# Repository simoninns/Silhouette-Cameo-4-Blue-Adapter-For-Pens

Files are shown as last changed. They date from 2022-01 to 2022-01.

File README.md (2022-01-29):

# Silhouette Cameo 4 Blue Adapter For Pens
## Overview
This is a 3D printable adapter for the Silhouette Cameo 4 equivalent to the blue adapter typically used to allow Silhouette pens to work in the Cameo 4 (why they don't work natively is anyone's guess...).

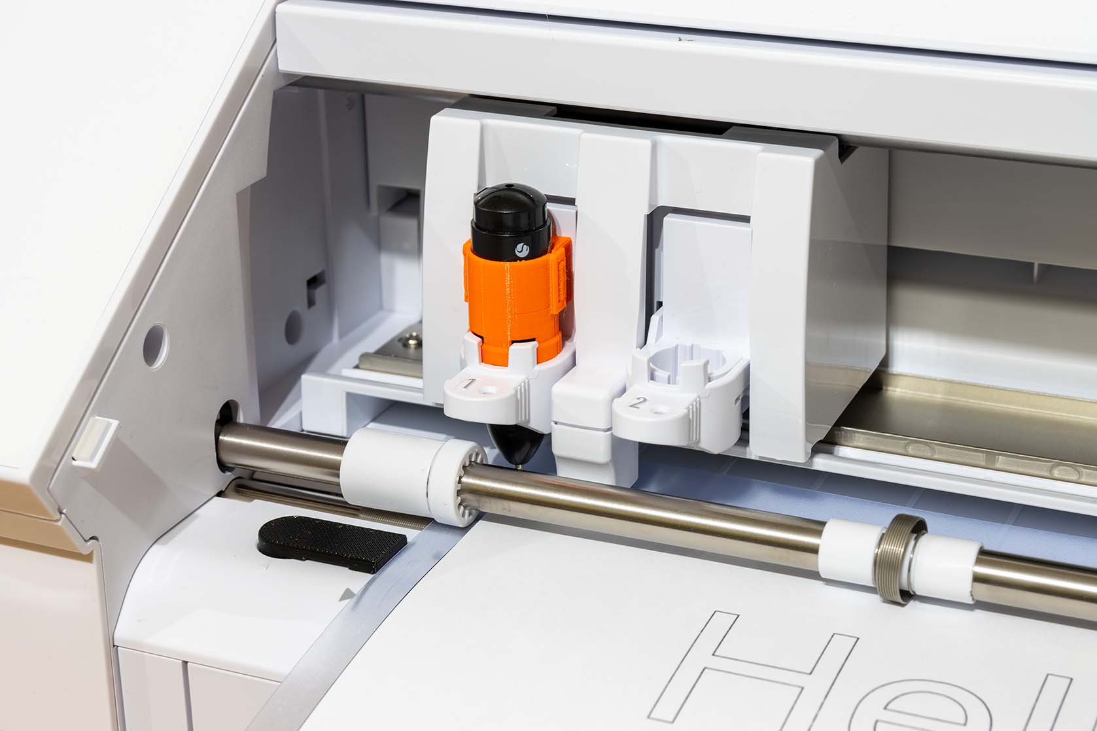
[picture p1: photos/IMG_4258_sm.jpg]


Since the original adapter is made from extremely thin plastic it is not possible to print the adapter without redesign.  This design relies on front and back guide pins to hold the pen square to the plotter rather than a thin plastic surround.  The pen is held rigidly and does not wobble during plotting. 

To make the design even more convenient there is a pen lid included so the pen does not need to be removed from the adapter when not in use; simply pop on the cap and store.

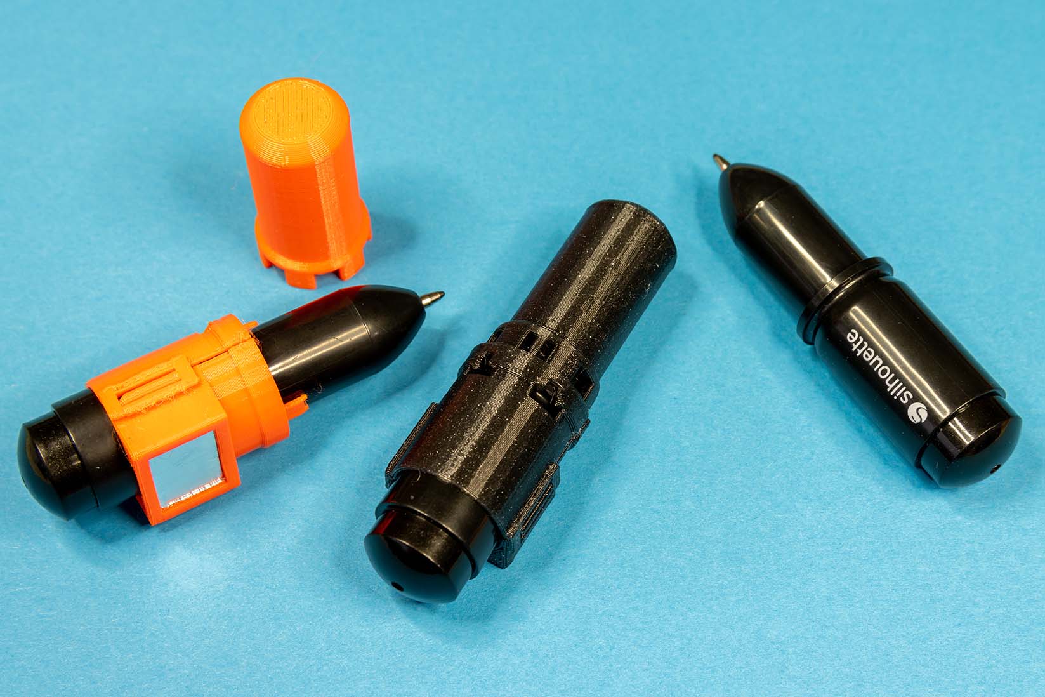
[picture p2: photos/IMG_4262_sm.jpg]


Note: This project is GPLv3 open-source. The github repository for the model (containing the complete OpenSCAD project) can be found at https://github.com/simoninns/silhouette-cameo-4-blue-adapter-for-pens

## Printing instructions
The model has been printed and tested on the Prusa MK3S/MMU2S printer using Prusament PETG filament. All parts fit on a 20x20 printing bed.

### Recommended print settings

Print settings (for Prusa Slicer) are the same for all included parts:

* Material: PETG
* Layer: 0.20mm (Quality)
* Infill: 15%
* Supports: No Supports

Note that the upper 'ring' of the front and back parts may string a little due to the lack of supports.  Simply trim this off after printing rather than using build-plate supports for quicker printing with less material.

## Assembly
Place the front part over the pen ensuring that the 'ring' is correctly seated. Then clip the back part in place one side at a time.  Finally, pop the cap on the top.  Now follow the tool auto-detection instructions below.

## Tool auto-detection
The Cameo 4 uses an automatic tool detection system which is based on the size of a rectangle of aluminum on the back of the tool.  The pen-holder design has a 14x10mm recess for the aluminum.

A Silhouette Studio file is included in the project that can be used to make the required aluminum.  Use 50mm wide aluminum tape (I used Tesa professional aluminum tape (strong) which is 50mm x 25m x 50 microns).  Aluminum tape is used in the heating/air con. industry so it's easy to source.

The included file uses the auto-blade with the following settings:

* Blade Depth: 4
* Force: 14
* Passes: 1
* Speed: 5

Simply cut about 150mm of aluminum tape and affix to a cutting board (make sure it's as smooth as possible). Then, after cutting, place 1 or 2 pieces (one on top of the other) in the provided recess on the tool.  The Cameo will then auto-detect the pen holder just like the manufacturer's original part.

## Author
The Silhouette Cameo 4 Blue Adapter For Pens is designed and maintained by Simon Inns.

# Licensing
## OpenSCAD source files - software license (GPLv3)

    This is free software: you can redistribute it and/or modify
    it under the terms of the GNU General Public License as published by
    the Free Software Foundation, either version 3 of the License, or
    (at your option) any later version.
    
    This program is distributed in the hope that it will be useful,
    but WITHOUT ANY WARRANTY; without even the implied warranty of
    MERCHANTABILITY or FITNESS FOR A PARTICULAR PURPOSE.  See the
    GNU General Public License for more details.
    
    You should have received a copy of the GNU General Public License
    along with this program.  If not, see <http://www.gnu.org/licenses/>.

## Non-source-code media - Creative Commons license (Creative Commons BY-SA 4.0)
Please see the following link for details: https://creativecommons.org/licenses/by-sa/4.0/

You are free to:

Share - copy and redistribute the material in any medium or format
Adapt - remix, transform, and build upon the material
for any purpose, even commercially.

This license is acceptable for Free Cultural Works.

The licensor cannot revoke these freedoms as long as you follow the license terms.

Under the following terms:

Attribution - You must give appropriate credit, provide a link to the license, and indicate if changes were made. You may do so in any reasonable manner, but not in any way that suggests the licensor endorses you or your use.

ShareAlike - If you remix, transform, or build upon the material, you must distribute your contributions under the same license as the original.

No additional restrictions - You may not apply legal terms or technological measures that legally restrict others from doing anything the license permits.

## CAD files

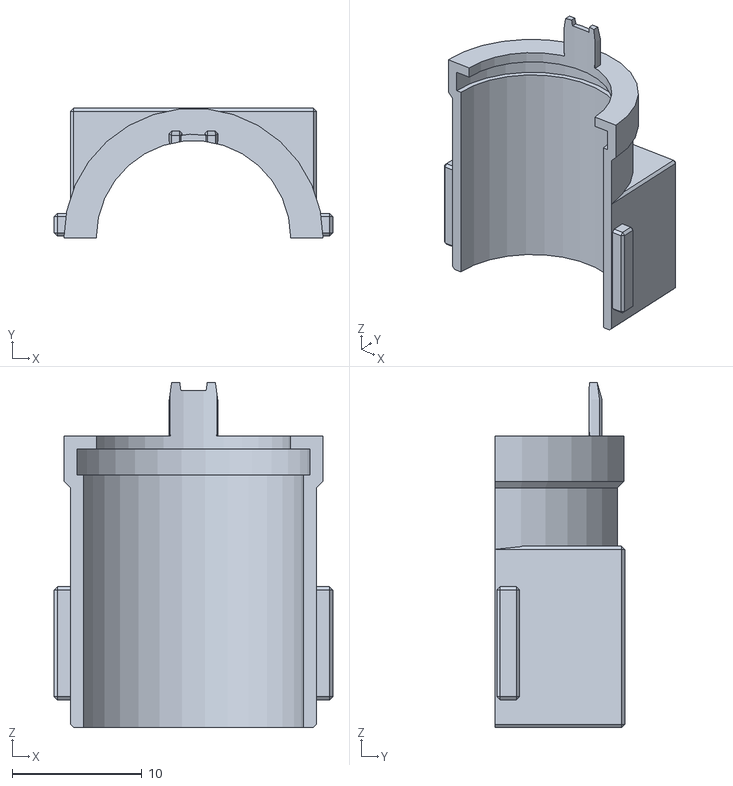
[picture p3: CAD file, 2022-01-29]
stl/blue_front.stl
21.5 x 10.0 x 26.6

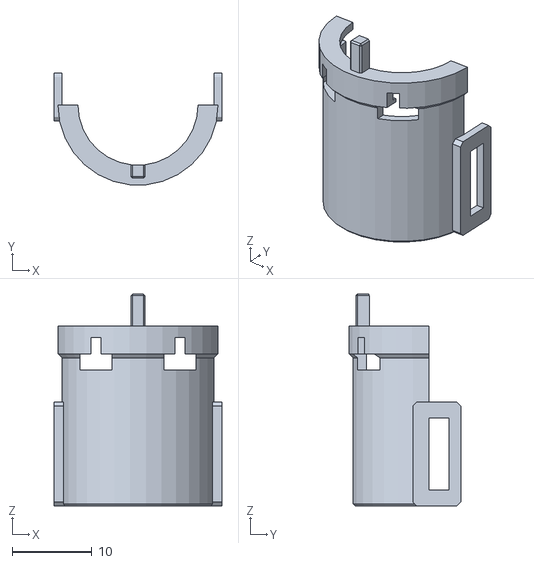
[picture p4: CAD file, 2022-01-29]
stl/blue_back.stl
21.0 x 13.9 x 26.5

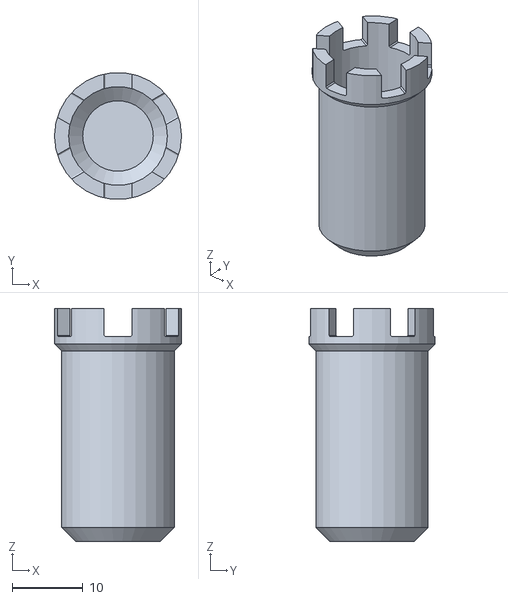
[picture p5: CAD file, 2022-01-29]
stl/blue_lid.stl
18.0 x 17.9 x 33.0

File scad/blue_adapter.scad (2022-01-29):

/************************************************************************

    blue_adapter.scad
    
    Silhouette Cameo 4 Adapters
    Copyright (C) 2022 Simon Inns
    
    This is free software: you can redistribute it and/or modify
    it under the terms of the GNU General Public License as published by
    the Free Software Foundation, either version 3 of the License, or
    (at your option) any later version.
    
    This program is distributed in the hope that it will be useful,
    but WITHOUT ANY WARRANTY; without even the implied warranty of
    MERCHANTABILITY or FITNESS FOR A PARTICULAR PURPOSE.  See the
    GNU General Public License for more details.
    
    You should have received a copy of the GNU General Public License
    along with this program.  If not, see <http://www.gnu.org/licenses/>.
	
    Email: simon.inns@gmail.com
    
************************************************************************/

include <BOSL/constants.scad>
use <BOSL/transforms.scad>
use <BOSL/shapes.scad>

module insertion_guide_front()
{
    // Insert guides
    move([0,7.75,27.5]) hull() {
        move([0,0,-4]) cuboid([1,1,4], chamfer=0.2);
        move([0,-0.5,-1]) cuboid([1.25 / 2,2.5 / 2,0.25]);
    }
}

module insertion_guide_back()
{
    // Insert guides
    move([0,-8,24]) cuboid([1.75,2.25,5], chamfer=0.2);
}

module tool_lock()
{
    difference() {
        union() {
            move([0,0,2.5]) {
                move([+5.25,0,21.5 - 4]) cuboid([1.25, 20, 2.1]);
                move([-5.25,0,21.5 - 4]) cuboid([1.25, 20, 2.1]);
            }

            move([0,0,17]) tube(h=2, od=20, , id=14, center=false);
        }

        move([0,0,17]) cuboid([6.5, 20, 6]);
        move([+10.5,0,17]) cuboid([6.5, 20, 6]);
        move([-10.5,0,17]) cuboid([6.5, 20, 6]);
        move([0,7,19]) cuboid([20, 10, 6]);
    }
}

module holder_body()
{
    // Base of holder
    difference() {
        union() {
            move([0,20/4,7]) cuboid([19,20/2,14], chamfer=0.25, edges=EDGES_TOP+EDGES_BOTTOM+EDGES_BACK);
            cyl(h=22.5, d=19, center=false, chamfer=0.25);

            move([0,0,16]) cyl(h=6.5, d=20, center=false, chamfer1=3);
        }

        move([0,10,14/2]) cuboid([14.2,2,10.2], edges=EDGES_TOP); // Alu marker recess
        tool_lock();
    }

    // Main Shaft
    move([0,0,21.5]) zrot(80) pie_slice(ang=20, l=4.5, d=16);
}

module inner_profile()
{
    // Base
    move([0,0,9 - 1]) cyl(h=24, d=17);

    // Ring
    move([0,0,20.5]) cyl(h=2, d=18);

    // Top
    move([0,0,17]) cyl(h=51, d=15);
}

module front_catches()
{
    move([-11 + 0.25,0.125,2.125]) cuboid([1.5,1.75,8.75], center=false, chamfer=0.25, edges=EDGES_X_ALL+EDGES_LEFT);
    move([9.25,0.125,2.125]) cuboid([1.5,1.75,8.75], center=false, chamfer=0.25, edges=EDGES_X_ALL+EDGES_RIGHT);
}

module back_catches()
{
    move([-14.5,-1,0]) {
        difference() {
            move([0,-1,0]) cuboid([1,6,13], center=false, chamfer=0.5, edges=EDGES_X_ALL);
            move([-1,1,2]) cuboid([3,2.5,9], center=false);
        }

        move([-0.75,-1,0]) cuboid([0.75,2,13], center=false, chamfer=0.5, edges=EDGES_X_FR);
    }

    move([-34.5,-1,0]) {
        difference() {
            move([0,-1,0]) cuboid([1,6,13], center=false, chamfer=0.5, edges=EDGES_X_ALL);
            move([-1,1,2]) cuboid([3,2.5,9], center=false);
        }

        move([0.75,-1,0]) cuboid([0.75,2,13], center=false, chamfer=0.5, edges=EDGES_X_FR);
    }
}

module render_blue_adapter_front(isDisplay)
{
    posy = isDisplay ? 0:6;

    move([0,posy,0]) {
        difference() {
            holder_body();
            inner_profile();

            // Cross section
            move([0,-10,25]) cuboid([20,20,60]);
        }

        // Insertion guides
        difference() {
            union () {
                move([+1.25 + 0.125,0,0]) insertion_guide_front();
                move([-1.25 - 0.125,0,0]) insertion_guide_front();
            }

            move([0,0,17]) cyl(h=51, d=15);
        }

        front_catches();
    }
}

module render_blue_adapter_back(isDisplay)
{
    posy = isDisplay ? 0:-6;
    move([0,posy,0]) {
            difference() {
            holder_body();
            inner_profile();

            // Cross section
            move([0,10,25]) cuboid([20,20,60]);
        }
        
        difference() {
            insertion_guide_back();
            move([0,0,17]) cyl(h=51, d=15);
        }

        move([24,0,0]) back_catches();
    }
}

module render_blue_adapter_lid(isDisplay)
{
    rota = isDisplay ? 0:180;
    priy = isDisplay ? 0:-55.5;

    yrot(rota) move([0,0,priy]) {
        difference() {
            union() {
                move([0,0,39]) cyl(h=33, d=16, chamfer2=2);
                move([0,0,26]) cyl(h=7, d=18, chamfer2=2);
            }
            move([0,0,39 - 1]) cyl(h=33, d=14, chamfer2=2);

            for(rota=[0: 360/6: 360]) {
                    rotate([0,0,rota]) move([0,-8,24]) cuboid([4,4,5], chamfer=0.2);
            }
        }
    }    
}

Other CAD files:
scad/main.scad
